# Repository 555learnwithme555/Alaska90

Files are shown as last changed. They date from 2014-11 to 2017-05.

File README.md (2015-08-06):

# Alaska90 3D printer design
This is the Alaska90, an enormous 3D printer.  It's not a tabletop machine--it's the size of a table!

Main features:
* 600mm x 500mm x 600mm build volume (24 inch x 20 inch x 24 inch), to construct models as big as a few feet on each side.
* Frame is built from 3/4 inch plywood, and parts are secured using large 1/4 inch hex head bolts (instead of M4 screws).
* Uses heavy 16mm steel rods, so it's rigid enough to mill wood with a small dremel tool.
* Support rods are moved inward, to gauss points, to better support the 24 inch x 24 inch bed.

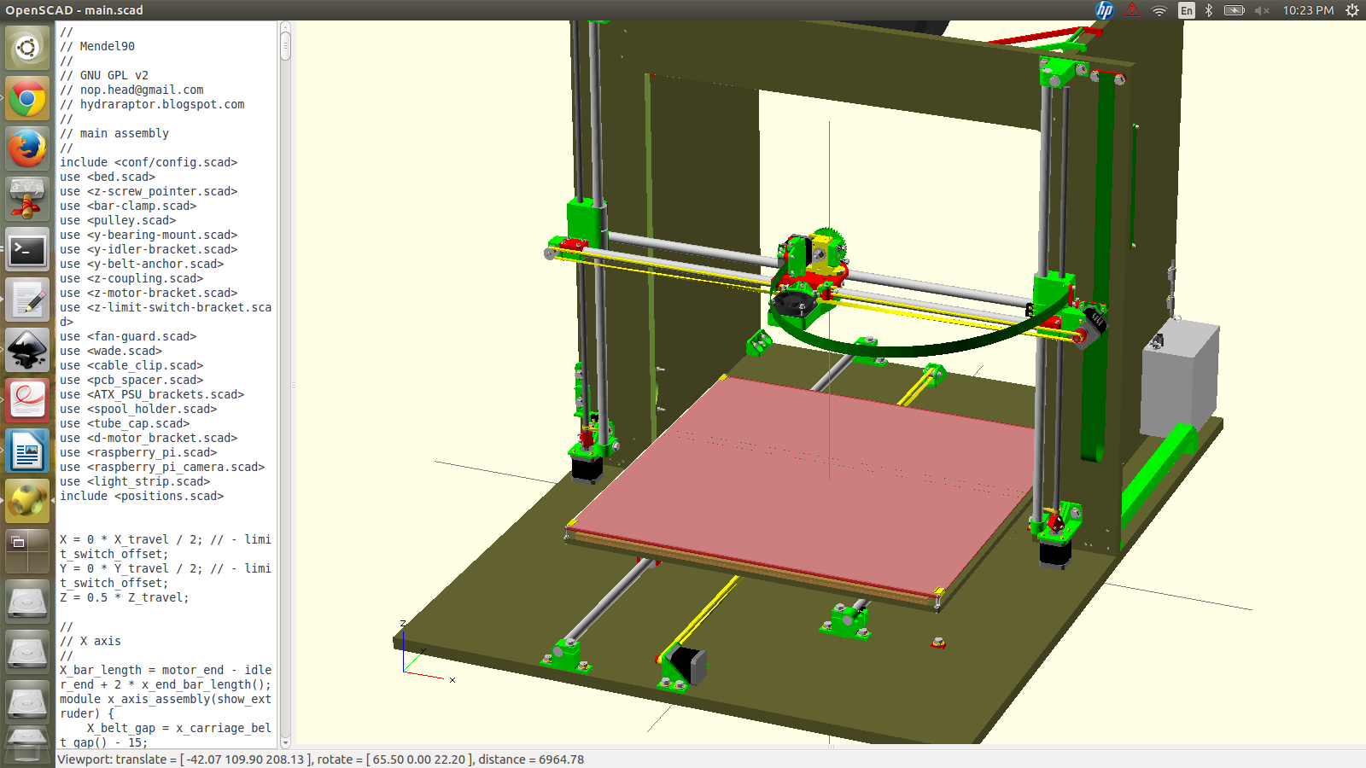
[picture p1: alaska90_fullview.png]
3D rendering of Alaska90 3D printer

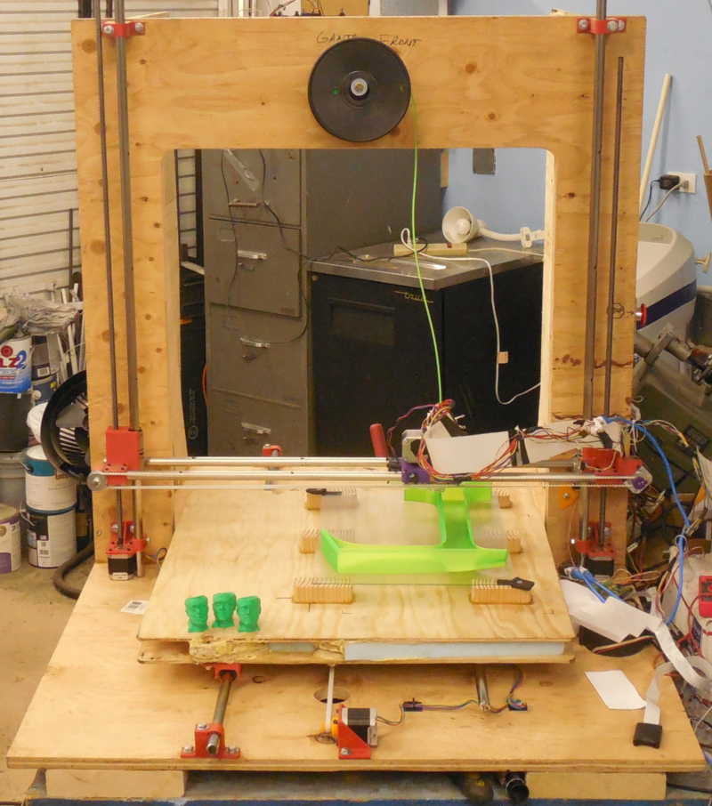
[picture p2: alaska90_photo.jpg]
Photograph of Alaska90 3D printer


This is an open source hardware design that started from Chris Palmer/nophead's amazing parametric CAD printer generator system Mendel90, with a number of changes by Dr. Orion Lawlor to accomodate the much larger machine.  This version is definitely "beta" quality, with several crude hacks in the OpenSCAD to make the STL parts work at the larger size.  Also, I laid out the frame holes by hand because I couldn't find a router big enough to cut the full 4ft x 3ft sheet, so the DXFs are likely to be somewhat inaccurate.

# Making giant 3D prints

There are a number of challenges in scaling up a 3D printer this big:

* Time per print.  At a fixed layer height, if you double the size of the object, the number of layers doubles, the time per perimeter doubles, and the time per infill quadruples.  This means the total time per print scales up quadratically even for completely hollow objects, and time is cubic for filled objects.  One workaround is to use large layer height, above 0.3mm, to reduce the number of layers.  You can also try to push the printer to deposit material faster by using a larger nozzle hole size, currently 0.5mm.
* Curl.  Without a heated bed and build chamber, a PLA object over a foot across will curl up off the build platform.

# Parts and suppliers

The original Mendel90 has a spectacularly detailed Bill-of-Materials (BOM) system that keeps track of every part needed, down to the last bolt and nut.  I tried to keep this updated--see [alaska90/bom/bom.txt](alaska90/bom/bom.txt)--but I probably didn't get it quite perfect, since much of the design was adapted on the fly.

## Mechanical parts & suppliers

I built the frame from 3/4" thick plywood, which I screwed and glued together rather than use 3D printed fixing blocks.  The base is built on an "H" shape of 2x8 lumber, glued to the base plywood, to increase stiffness and keep the machine up off the floor.

To reduce the moving mass of the bed while keeping it stiff, it was glued together as a "sandwich" with 5mm plywood on the top and bottom surfaces, and 1 inch thick blue XPS foam glued in the middle using one-part moisture cure urethane "Gorilla" glue.

http://www.amazon.com/LM16UU-Linear-Bearing-Bushing-linear/dp/B00AGCT6FW
	LM16UU linear bearings, one package of ten for $28

You need a total of six very straight and smooth steel rods:
	Two X axis rods, length 830mm (33 inches)
	Two Y axis rods, one long rod of length 1210mm (48 inches), and one short rod of length 692mm (28 inches).
	Two Z axis rods, length 760mm (30 inches)
Ideally, you'd start with five 36 inch rods (this is the standard length for "drill rod"), and add one 48 inch rod.

http://www.vxb.com/page/bearings/PROD/kit1008
	16mm hardened rod, 60" for $50.

I used 5/8 inch steel rods from an old foosball machine, which works since 5/8 inch is 15.83mm, but 16mm steel rods would fit the bearings with slightly less play.  In a machine this huge, deflection is going to dominate your positioning errors anyway.

http://smile.amazon.com/Rolled-Steel-Mandrel-Tubing-Length/dp/B000H9K3GU/
	5/8" OD, 0.40" ID, DOM and very smooth.  $15 for 36".

For the Z axis threaded rods, I used some 3/8 inch ACME threaded rod.  Normal 3/8 inch or 10mm threaded rod would probably work about equally well.

For the X and Y axes, I used T5 belts.  The cool kids are using GT2 belts nowadays, though!

http://smile.amazon.com/Meters-Timing-Perfect-RepRap-Mendel/dp/B00GVAOOUK/r
	5 meters T5 timing belt, $20

http://www.ebay.com/itm/T5-Aluminum-Timing-Pulleys-8-Tooth-5mm-Bore-for-RepRap-Prusa-Mendel-3D-Printer-/141217630049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
	T5 timing belt pulleys, 8 tooth, 5mm bore, $5

##Electrical Parts & Suppliers

You need five NEMA 17 stepper motors.  I was surprised to find the smaller steppers are quite strong enough to move this large machine, especially the Y axis, which needs to rapidly move a 10 pound table!

http://smile.amazon.com/gp/product/B00C43IW4C?psc=1&redirect=true&ref_=oh_aui_detailpage_o09_s00
	5x Kysan 1124090 stepper motors for $75

http://www.ebay.com/itm/0-3-0-35-0-4-0-5mm-Nozzle-for-RepRap-1-75-3mm-filament-J-Head-Jhead-MK-V-Hot-End-/361088211963
	$25 Ebay J-head hotend.  I picked 3mm filament and 0.5mm nozzle.

http://www.ebay.com/itm/Melzi-2-0-1284P-Reprap-Control-Mainboard-3-D-Printer-Controller-Main-Board-PCB-/121477844641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
	I used this $42 [Melzi controller board](http://reprap.org/wiki/Melzi).  
	
All the [stepper current limit potentiometers need to be cranked all the way](http://reprap.org/wiki/RepRapPro_Setting_Motor_Currents) for the tiny steppers to successfully push this large machine.  The Melzi stepper drivers tend to overheat when worked this hard, so I added a small squirrel cage fan blowing directly on them.

For printing PLA, I added a tiny 40mm case fan hanging between the X axis rods, by screwing M4 screws directly into the carriage.

I used a scrapped PC power supply to supply 12 volts (yellow and black wires) to the Melzi.  I added a big red emergency stop button to disconnect the power supply's green power-on wire from ground, turning the power supply off.

Much to my detriment, for my wiring I used a combination of rats-nest hand assembled wire bundles, which are messy and confusing; and RJ45 connectors, which are not very good at handling the 2-3 amp current to the steppers and hotend.  Nophead designed in neat brackets for ribbon cable, which would probably work better.

-------------------------- Original Mendel90 README -------------------
Limitations
-----------
Currently only supports mendel and sturdy machine variants, the huxley version needs more work.

Use
---
Add the directory of the OpenScad executable to your search path. OpenSCAD-2013.06 or later is required.
To get PDF versions of the sheet drawings add InkScape to your search path.

To make all the files for a machine run
```python
make_machine.py machine_name
```

To make just the bom, sheets or stls run bom.py, sheets.py or stls.py machine\_name.

machine\_name can be mendel or sturdy. To make your own variant copy scad\conf\mendel\_config.scad or scad\conf\sturdy\_config.scad to yourname\_config.scad.  Then run `make_machine.py yourname`.

To view the model of the whole machine, open scad\main.scad. It will take several minutes to render (about about 8 minutes on my computer) but after that you can pan and zoom it at reasonable speed and changes takes less time to render.  (Note: main.scad will only render correctly if conf\machine.scad exists, which is created by the make_machine.py script.)

To view a sub-assembly, open the individual scad files. Set the exploded flag in config.scad to make exploded views.

To get blender renders of all the parts put blender in your search path and run `render.py machine_name`.

Credits
-------
Fan model based on [this model](http://www.thingiverse.com/thing:8063) by MiseryBot, CC license.

[Sanguinololu model](http://www.thingiverse.com/thing:18606) by ax\_the\_b, CC license.

Spring taken from openscad example 20

x-end.scad and wade.scad use some elements of the Prusa ones by Josef Prusa, GPL license.

z_couplings originally based on [this model](http://www.thingiverse.com/thing:7153) by Griffin_Nicoll, GPL license.

Bearing holders originally based on [this model](http://www.thingiverse.com/thing:7755) by Jolijar, CC license.

InkCL.py based on [this code](http://kaioa.com/node/42)

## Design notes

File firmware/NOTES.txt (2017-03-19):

Flashing Alaska90 firmware to Melzi 2.0 board works like a 
"sanguino" arduino:
	- Use Arduino IDE 1.0.5:  ~/dev/hardware/arduino/ide/old/arduino-1.0.5/arduino

In 1.6.5, go to File -> Preferences -> Additional board manager URLs:
  https://raw.githubusercontent.com/Lauszus/Sanguino/master/package_lauszus_sanguino_index.json
Now go to Tools -> Boards -> Boards Manager. 
Scroll to the bottom, and "Install" the Sanguino.

Tools -> Boards -> Sanguino
Tools -> Processors -> ATmega 1284 or 1284P 16MHz

---------- The Hardware ---------
Sanguino (open source, ATmega 644P)
-> Sanguilino (includes steppers)
-> Melzi ("Joe Mosfet", ATmega 1284P, like Leonardo)
-> Melzi 2.0 (RepRapPro)

This is basically an Arduino Leonardo (ATMEGA1284P), with four A4988 stepper drivers (2A, 35V rated), and three RFP30N06LE MOSFETs (30A, 60V rated).  You use the Marlin/Sanguino firmware.
	http://reprap.org/wiki/Melzi

Must copy the Marlin_official/ArduinoAddons/Arduino_1.x.x/hardware/Sanguino directory into the arduino IDE/hardware folder (as of 1.0.5) for the Sanguino boards to show up.  Pick board "Sanguino W/ ATmega 1284p 16(?)MHz".
This only seems to work with the 1.0.5 IDE, not 1.6.x.

To edit the Melzi firmware, you need to install the AUTO-RESET jumper on the right side of the board.

http://www.youtube.com/watch?v=PQ807R1Nsio
Quint Boney uses Repetier Firmware on Melzi 2.0 electronics.

------------- Marlin --------------
Default baudrate is 250000.  Dropping to 115200.

eBay J clone Thermistor:
	57F -> 165 K ohms
	72F -> 100 K ohms
This crappy board's pull-up is 10Kohms, so I needed to manually adjust the table using the thermistor.xls spreadsheet.  I have no idea how close it is when hot, but it's pretty close when cold.  Using a 1K pull-up would be better, since the hot end 

Heater resistor: 12ohms, so about 12 watts at 12VDC.

The normal Arduino IDE flashes the firmware fine, although it takes a scary length of time to flash, and the LED no longer blinks.

pronterface takes an amazing 8 seconds to connect.
Using a 1K resistor as a fake thermistor results in a temperature reading of 198.4/5 C in Pronterface.  It should actually be 172.5 C, according to my thermistor table.  I need to meter the "10K" pullup to see what it really reads.  Turns out, it's like 9.8Kohms, but the problem was selecting the right table in Configuration.h.  With the right table, we're at 173.9/174.2, which is perfect.

Z speed: seems capped at 300mm/min (pretty slow!).  Fixed in firmware DEFAULT_MAX_FEEDRATE.

At acceleration of 100:
Up to 460mm/min works OK.
Z loses steps going up at 500, 600, or 700 mm/min.

At acceleration of 20, acceleration process is audible.  Steps still lost at 560 (only going up, and only now and then), and more definitely at 660.

Capping Z speed to 7 mm/sec, 460mm/min.  That's still over 1 minute for a full Z seek, but OK.

-------
To tune hotend:

M303 E0 S200 C4

---------------
I'd like to set up a sub-Melzi to drive the sandstruder.

I'm tempted to just tie across pin A1 from the mainmelzi to the submelzi.
Main would have it as the E1 step pin; sub would forward it to E0.
(sandstruder doesn't really do retract.)

~/dev/hardware/arduino/ide/old/arduino-1.0.5/arduino subMelzi/subMelzi.ino

The Melzi board bootloader(?) really does take 8 seconds to boot.  That's annoying.

-----------------
Two extruders is surprisingly easy to set up, and it works well.
Three extruders, E2 randomly dribbles whenever E1 is stepping.
Is this because "DIR" pins overlap for T1 and T2 somehow?

Trying to separate the T1 and T2 pins by more distance:
// Sub-melzi extruder 1: sandstruder
#define E1_STEP_PIN      30 // pin analog A1 (fake fastio.h pin numbers)
#define E1_DIR_PIN       29 // pin analog A2
#define E1_ENABLE_PIN      -1

// Sub-melzi extruder 2: tamper
#define E2_STEP_PIN      27 // pin analog A4
#define E2_DIR_PIN       28 // pin analog A3
#define E2_ENABLE_PIN      -1

---------------
Bumped up to 24V operation.  Re-tuning moves:

http://marlinfw.org/docs/gcode/M203.html

Dump current settings with M503

echo:Steps per unit:
echo:  M92 X53.33 Y53.33 Z1511.79 E519.11
echo:Maximum feedrates (mm/s):
echo:  M203 X600000.00 Y600000.00 Z10.00 E100.00
echo:Maximum Acceleration (mm/s2):
echo:  M201 X600000 Y600000 Z1000 E5000
echo:Acceleration: S=acceleration, T=retract acceleration
echo:  M204 S3000.00 T3000.00
echo:Advanced variables: S=Min feedrate (mm/s), T=Min travel feedrate (mm/s), B=minimum segment time (ms), X=maximum XY jerk (mm/s),  Z=maximum Z jerk (mm/s),  E=maximum E jerk (mm/s)
echo:  M205 S0.00 T0.00 B20000 X3.00 Z0.40 E3.00
echo:Home offset (mm):
echo:  M206 X0.00 Y0.00 Z0.00
echo:PID settings:
echo:   M301 P10.20 I0.63 D40.00

M201 sets max acceleration (mm/sec^2)
M203 sets max feedrate (mm/sec)

g1 x200 y200 f20000

'f' moves are mm/minute
firmware numbers are mm/second, off by 60x

Crazy fast, but still doesn't seem to lose steps at 19.6VDC:
M201 X60000 Y60000
M203 X60000 Y60000
g1 f60000
g1 x200 y200
g1 x300 y300

M201 X600000 Y600000

Too fast: loses steps at peak velocity:
M203 X600000 Y600000

Good and fast: 
M203 X60000 Y60000

g1 f600000
g1 x200 y200
g1 x300 y300

Noticably slower:
M201 X600 Y600

Slow ramp-up:
M201 X60 Y60

Actual active acceleration seems to be the M204:
At 19.6V, empty bed:
  M204 S60000 ; uncapped

Conservative:
M201 X3000 Y1000 Z100 E
M203 X1000 Y1000 Z8   E
Midrange:
M201 Y1500 X5000 

Y change: 
M201 Y1000
M203 Y1100 
G1 F100000
G1 Y100 
G1 Y400
velocity:
1100 fine
5000 fine (never hits peak at 1000 accel)

accel:
1000 slow and careful (correct long-term speed)
2000 might lose one occasional step
2300 loses a tiny block of steps at each run (and still loses a few at 24V)
2500 loses a few steps
3000 loses most steps
10000 loses all steps in Y axis

X change:
M201 X5000
M203 X1100 
G1 F100000
G1 X100 
G1 X400
vel:
1000 fine
1100 fine
1200 loses steps in big clunky chunks (?!)
2000 loses steps
5000 loses steps
accel:
1000 slow and fine
3000 fine
5000 seems reliable
6000 still reliable
7000 loses on return
10000 loses most steps

Z change: big limit is feedrate
M201 Z100
M203 Z8 
G1 Z110
G1 Z130
Acceleration M201 Z10 is very slow. Z100 is about normal.  Z1000 looks same.
Feedrate M203 Z100 moves too fast
8 is probably safe
10 is fine
12, 13, 15 lose steps (!)
20 hits resonance and loses steps

Actual used acceleration is smaller of:
  M204 Sxxxx global limit (combined X and Y?)
  M203 per-axis limit

Right thing is probably to leave S big, do work per-axis.

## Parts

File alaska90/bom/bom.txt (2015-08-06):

Vitamins:
          E                                                      
          x                                                      
          t                                                      
          r                                                      
          u                                                      
          d                                                      
          e                                                      
          r                                                      
                                                                 
          c  E                       X                       Z   
          o  x                                                   
          n  t              S        c                       l   
    E     n  r              p        a                       i   
    l     e  u              o     X  r           Y           m   
    e     c  d        P     o        r                       i   
    c  E  t  e        r     l     c  i           c           t   
 B  t  x  i  r     M  i           a  a  X  X     a  Y  Y        Z
 e  r  t  o        a  n     h  X  r  g        Y  r        Z  s   
 d  o  r  n  m  F  c  t     o     r  e  i  m     r  i  m     w  m
    n  u     o  r  h        l  a  i     d  o  a  i  d  o  a  i  o
 f  i  d  p  t  a  i  b  P  d  x  a  f  l  t  x  a  l  t  x  t  t
 a  c  e  c  o  m  n  e  s  e  i  g  a  e  o  i  g  e  o  i  c  o
 n  s  r  b  r  e  e  d  u  r  s  e  n  r  r  s  e  r  r  s  h  r
  |  |  |  |  |  |  |  | 1|  |  |  |  |  |  |  |  |  |  |  |  |  |  1 THS15 Aluminium clad resistor 10R
  |  |  |  |  |  |  |  | 1|  |  |  |  |  |  |  |  |  |  |  |  |  |  1 THS15 Aluminium clad resistor 4R7
  |  |  |  |  |  |  |  | 1|  |  |  |  |  |  |  |  |  |  |  |  |  |  1 PSU e.g. ALPINE500
  |  | 3|  |  |  |  |  |  | 4|  |  |  |  |  |  |  |  |  |  |  |  |  7 Ball bearing 608 8mm x 22mm x 7mm
  |  |  |  |  |  |  |  |  |  |  |  |  | 2|  |  |  | 2|  |  |  |  |  4 Ball bearing 624 4mm x 13mm x 5mm
  |  |  |  |  |  |  | 4|  |  |  |  |  |  |  |  |  |  |  |  |  |  |  4 19mm bulldog clip
  |  |  |  |  |  |  | 1|  |  |  |  |  |  |  |  |  |  |  |  |  |  |  1 PCB bed 615mm x 615mm
  |  |  |  |  |  |  |  |  |  | 1|  |  |  |  |  |  |  |  |  |  |  |  1 Belt T5 x 6mm x 1760mm
  |  |  |  |  |  |  |  |  |  |  |  |  |  |  | 1|  |  |  |  |  |  |  1 Belt T5 x 6mm x 1820mm
  |  |  |  |  |  |  | 2|  |  |  |  |  |  |  |  |  |  |  |  |  |  |  2 Corrugated cardboard 578mm x 618mm x 5mm
  |  |  |  |  |  |  | 4|  |  |  | 2|  |  |  |  |  |  |  |  |  |  |  6 M3 cap screw x 10mm
  |  | 3|  |  |  |  |  |  |  |  |  |  |  | 6|  | 8|  |  |  |  |  | 17 M3 cap screw x 16mm
  |  |  |  |  |  |  |  |  |  |  | 1|  |  | 2|  |  |  |  |  |  | 8| 11 M3 cap screw x 20mm
  | 4|  |  |  |  |  |  |  |  |  | 2|  |  |  |  |  |  |  |  |  |  |  6 M3 cap screw x 25mm
  |  |  |  |  |  |  |  |  |  |  |  |  | 8| 8|  |  |  |  |  |  |  | 16 M3 cap screw x 30mm
  |  |  |  | 2|  |  |  |  |  |  |  |  |  | 1|  |  |  |  |  |  |  |  3 M3 cap screw x 45mm
  |  |  |  |  |  |  |  |  |  |  |  | 4|  |  |  |  | 1|  |  |  |  |  5 M4 cap screw x 30mm
 4|  |  |  |  |  |  |  |  |  |  |  |  |  |  |  |  |  |  |  |  |  |  4 M4 cap screw x 35mm
  |  |  |  |  |  |  |  |  |  |  |  |  | 1|  |  |  |  |  |  |  |  |  1 M4 cap screw x 45mm
  |  |  | 1|  |  |  |  |  |  |  |  |  |  |  |  |  |  |  |  |  |  |  1 15 way D PCB mount plug
  |  |  |  |  |  |  |  |  |  |  |  |  |  | 1|  |  |  |  |  |  |  |  1 15 way D IDC socket
  |  |  |  |  |  |  |  |  |  |  |  | 1|  |  |  |  |  |  |  |  |  |  1 Fan 60mm x 15mm
  |  |  |  |  |  |  |  |  | 1|  |  |  |  |  |  |  |  |  |  |  |  |  1 Foam sponge 20mm x 20mm x 20mm
  |  |  |  | 1|  |  |  |  |  |  |  |  |  | 1|  |  |  | 1|  |  |  |  3 M3 grub screw x 6mm
  |  |  |  |  |  |  | 1|  |  |  |  |  |  |  |  |  |  |  |  |  |  |  1 Glass sheet 615mm x 603mm x 2mm
  |  |  |  |  |  |  | 4|  |  |  |  |  |  |  |  |  |  |  |  |  |  |  4 Hex male / female pillar M6.5 x 13mm
  |  | 3|  |  |  |  |  |  |  |  |  |  |  |  |  |  |  |  |  |  |  |  3 M3 hex screw x 10mm
  |  |  |  |  |  |  |  |  |  |  |  |  |  |  |  |  |  |  |  | 1|  |  1 M3 hex screw x 16mm
  |  | 2|  |  |  |  |  |  |  |  |  |  |  |  |  |  |  |  |  |  |  |  2 M4 hex screw x 20mm
  |  | 2|  |  |  |  |  |  |  |  |  |  |  |  |  |  |  |  |  |  |  |  2 M4 hex screw x 50mm
  |  | 1|  |  |  |  |  |  |  |  |  |  |  |  |  |  |  |  |  |  |  |  1 M8 hex screw x 60mm, hobbed at 25
  |  |  |  |  |  |  |  | 1|  |  |  |  |  |  |  |  |  |  |  |  |  |  1 IEC mains lead
  |  |  |  |  |  |  |  |  |  |  |  |  |  |  |  | 6|  |  |  |  |  |  6 1/4in hex screw x 16mm
  |  |  |  |  |  |  |  |  |  |  |  |  |  |  |  | 2|  |  |  |  |  |  2 1/4in hex screw x 20mm
  |  |  |  |  |39|  |  | 4| 2|  |  |  |  |  |12|  | 1| 4| 6| 2| 6| 76 1/4in hex screw x 25mm
  |  |  |  |  |  |  |  |  |  |  | 1|  | 2| 2|  | 3|  |  |  |  |  |  8 LM16UU linear bearing
  |  |  |  |  |  |  |  |  |  |  |  |  |  |  |  | 1|  |  |  |  |  |  1 MDF sheet 618mm x 618mm x 10mm
  |  |  |  |  | 2|  |  |  |  |  |  |  |  |  |  |  |  |  |  |  |  |  2 MDF sheet 532mm x 809mm x 19.5mm
  |  |  |  |  | 1|  |  |  |  |  |  |  |  |  |  |  |  |  |  |  |  |  1 MDF sheet 916mm x 1213mm x 19.5mm
  |  |  |  |  | 1|  |  |  |  |  |  |  |  |  |  |  |  |  |  |  |  |  1 MDF sheet 916mm x 809mm x 19.5mm
  | 1|  |  |  |  |  |  |  |  |  |  |  |  |  |  |  |  |  |  |  |  |  1 Melzi electronics
  |  |  | 1|  |  |  |  |  |  |  |  |  |  |  |  |  |  |  |  |  |  |  1 2 way Molex KK header
  |  |  | 1|  |  |  |  |  |  |  |  |  |  |  |  |  |  |  |  |  |  |  1 3 way Molex KK header
  |  |  |  | 1|  |  |  |  |  |  |  |  |  | 1|  |  |  | 1|  |  | 2|  5 NEMA17 x 48mm stepper motor
  |  |  |  |  |  |  |  |  |  |  |  |  |  |  |  |  |  |  | 2|  |  |  2 Brass nut M8
  |  | 3|  | 3|  |  |  |  |  |  | 1|  |  | 1|  |  |  | 1|  |  |  |  9 Nut M3
  |  | 2|  |  |  |  |  |  |  |  |  |  |  |  |  |  |  |  |  |  |  |  2 Nut M4
  |  | 2|  |  |  |  |  |  |  |  |  |  |  |  |  |  |  |  |  |  |  |  2 Nut M8
  |  |  |  |  |  |  |  |  |  |  | 4|  | 8|14|  | 8|  |  |  | 1| 8| 43 Nyloc nut M3
 4|  |  |  |  |  |  |  |  |  |  |  | 4| 1|  |  |  | 1|  |  |  |  | 10 Nyloc nut M4
  |  |  |  |  |  |  |  |  |  |  |  |  |  |  | 4| 8|  |  | 2|  | 2| 16 Nyloc nut M6.4
  |  |  |  |  |  |  |  |  |  |  |  |  |  | 2|  |  |  |  |  |  |  |  2 Nitrile O-ring 2.5mm x 1.6mm
  |  |  | 1|  |  |  |  |  |  |  |  |  |  |  |  |  |  |  |  |  |  |  1 Extruder connection PCB
  |  |  |  |  |  |  |  |  | 1|  |  |  |  |  |  |  |  |  |  |  |  |  1 PLA sample 3mm ~50m
  |  |  |  |  |  |  |  |  |  |  |  |  |  | 1|  |  |  |  |  |  |  |  1 Polypropylene strip 793mm x 18mm x 0.5mm
  |  |  |  |  |  |  |  |  |  |  |  |  |  | 1|  |  |  |  |  |  |  |  1 Polypropylene strip 984mm x 25mm x 0.5mm
  |  |  |  |  |  |  | 1|  |  |  |  |  |  |  |  |  |  |  |  |  |  |  1 Polypropylene strip 466mm x 33mm x 0.5mm
  |  |  |  |  |  |  |  |  |  |  |  |  |  | 2|  |  |  | 4|  |  | 8| 14 M3 pan screw x 8mm
  |  |  |  |  |  |  |  | 2|  |  |  |  |  |  |  |  |  |  |  |  |  |  2 6-32 pan screw x 9.5mm
  |  |  |  | 2|  |  |  | 4|  |  |  |  |  | 4| 2|  |  |  |  | 2|  | 14 No2 pan wood screw x 13mm
  |  |  |  |  |  |  |  |  |  |  |  |  |  | 1|  |  |  |  |  |  |  |  1 Ribbon cable 20 way 2147mm
  |  |  |  |  |  |  | 1|  |  |  |  |  |  |  |  |  |  |  |  |  |  |  1 Ribbon cable 26 way 576mm
  |  |  |  |  |  |  |  |  |  |  |  |  |  |  | 1|  |  |  |  |  |  |  1 Smooth rod 16mm x 1209mm
  |  |  |  |  |  |  |  |  |  |  |  |  |  |  | 1|  |  |  |  |  |  |  1 Smooth rod 16mm x 692mm
  |  |  |  |  |  |  |  |  |  |  |  |  |  |  |  |  |  |  | 2|  |  |  2 Smooth rod 16mm x 759mm
  |  |  |  |  |  |  |  |  |  | 2|  |  |  |  |  |  |  |  |  |  |  |  2 Smooth rod 16mm x 829mm
  |  | 1|  |  |  |  |  |  |  |  |  |  |  |  |  |  |  |  |  |  |  |  1 Smooth rod 8mm x 22mm
  | 1|  |  |  |  |  |  |  |  |  |  |  |  |  |  |  |  |  |  |  |  |  1 Micro SD card
  | 1|  |  |  |  |  |  |  |  |  |  |  |  |  |  |  |  |  |  |  |  |  1 Micro SD to USB adapter
  |  |  |  |  |  |  |  |  |  |  |  |  |  | 1| 1|  |  |  |  | 1|  |  3 Microswitch
  |  | 2|  |  |  |  |  |  |  |  |  |  |  |  |  |  |  |  |  |  |  |  2 Spring 7mm OD, 1mm gauge x 10mm long
  |  |  |  |  |  |  |  |  |  |  |  |  |  |  |  |  |  |  | 2|  |  |  2 Threaded rod M9.5 x 711mm
  |  |  |  |  |  |  |  | 1|  |  |  |  |  |  |  |  |  |  |  |  |  |  1 Heatshrink sleeving ID 10mm x 15mm
  |  |  |  |  |  |  | 2|  |  |  |  |  |  |  |  |  |  |  |  |  |  |  2 Heatshrink sleeving ID 1.6mm x 15mm
  | 2|  |  |  |  |  | 2| 3|  |  |  |  |  | 4|  |  |  |  |  |  |  | 11 Heatshrink sleeving ID 2.4mm x 15mm
  |  |  |  |  |  |  |  | 5|  |  |  |  |  |  |  |  |  |  |  |  |  |  5 Heatshrink sleeving ID 3.2mm x 15mm
  |  |  |  |  |  |  |  |  | 1|  |  |  |  |  |  |  |  |  |  |  |  |  1 PTFE tubing OD 4.6mm ID 3.84mm x 750mm
  |  |  |  |  |  |  |  | 2|  |  |  |  |  |  |  |  |  |  |  |  |  |  2 Heatshrink sleeving ID 6.4mm x 15mm
  |  |  |  |  |  |  | 2|  |  |  |  |  |  |  |  |  |  |  |  |  |  |  2 Heatshrink sleeving ID 6.4mm x 30mm
  |  |  |  |  |  |  |  |  |  |  |  |  |  |  |  |  |  |  |  |  | 2|  2 Neoprene tubing OD 8mm ID 5mm x 16mm
  |  |  | 2|  |  |  |  |  |  |  |  |  |  |  |  |  |  |  |  |  |  |  2 4 way terminal block
  |  |  |  |  |  |  | 1|  |  |  |  |  |  |  |  |  |  |  |  |  |  |  1 Epcos B57861S104F40 100K 1% thermistor
  | 1|  |  |  |  |  |  |  |  |  |  |  |  |  |  |  |  |  |  |  |  |  1 USB A to Mini B lead
  |  |  |  | 2|  |  |  |  |  |  |  |  |  | 4| 2|  |  |  |  | 2|  | 10 Washer M2.5 x 5.9mm x 0.5mm
  | 4| 3|  | 2|  |  | 4|  |  |  | 4|  | 8|21|  | 8|  | 4|  | 1|16| 75 Washer M3 x 7mm x 0.5mm
 4|  | 7|  |  |  |  |  | 2|  |  |  | 4| 2|  |  |  | 4|  |  |  |  | 23 Washer M4 x 9mm x 0.8mm
  |  |  |  |  |  |  |  |  |  |  |  |  | 2|  |  |  | 2|  |  |  |  |  4 Washer M5 x 20mm x 1.4mm
  |  |  |  |  |39|  |  | 4|14|  |  |  |  |  |12|14| 1| 4| 6| 2| 6|102 Washer M8 x 17mm x 1.6mm
  |  |  |  |  |  |  |  |  | 4|  |  |  |  |  |  |  |  |  |  |  |  |  4 Washer M8 x 30mm x 1.5mm
  |  |  |  |  |  |  |  |  |  | 2|  |  |  |  |  |  |  |  |  |  |  |  2 Wingnut M4
  |  |  |  |  |  |  |  |  |  |  |  |  |  |  |  |  |  |  |  | 2|  |  2 Rubber washer M3 x 10mm x 1.5mm
  |  |  |  |  |  |  | 1|  |  |  |  |  |  |  |  |  |  |  |  |  |  |  1 Black wire 32/0.2 length 635mm
  |  |  |  |  |  |  | 1|  |  |  |  |  |  |  |  |  |  |  |  |  |  |  1 Red wire 32/0.2 length 620mm
  | 4| 6|  |  |  |  |  |  |  |  |  |  |  | 2|  |  |  | 4|  |  | 8| 24 Star washer M3 x 0.5mm
  |  |  |  |  |  |  |  | 2|  |  |  |  |  |  |  |  |  |  |  |  |  |  2 Star washer M4 x 0.8mm
  |  | 1|  |  |39|  |  | 4| 2|  |  |  |  |  | 8|  | 1| 4| 4| 2| 4| 69 Star washer M8 x 1.6mm
  |  |  |  |  |  |  |  | 2|  |  |  |  |  |  |  |  |  |  |  |  |  |  2 Ziptie 100mm min length
  |  |  |  |  |  |  |  |  |  |  | 3|  |  |  |  | 3|  |  |  |  |  |  6 Ziptie 140mm min length

Printed:
  |  |  |  |  |  |  |  | 1|  |  |  |  |  |  |  |  |  |  |  |  |  |  1 atx_long_bracket.stl
  |  |  |  |  |  |  |  | 1|  |  |  |  |  |  |  |  |  |  |  |  |  |  1 atx_short_bracket.stl
  |  |  |  |  | 2|  |  |  |  |  |  |  |  |  |  |  |  |  |  |  |  |  2 cable_clip_AB.stl
  |  |  |  |  | 2|  |  |  |  |  |  |  |  |  |  |  |  |  |  |  |  |  2 cable_clip_AD.stl
  |  |  |  |  | 1|  |  |  |  |  |  |  |  |  |  |  |  |  |  |  |  |  1 cable_clip_CA.stl
  |  |  |  | 1|  |  |  |  |  |  |  |  |  |  |  |  |  |  |  |  |  |  1 d_motor_bracket.stl
  |  |  |  | 1|  |  |  |  |  |  |  |  |  |  |  |  |  |  |  |  |  |  1 d_motor_bracket_lid.stl
  |  |  |  |  |  |  |  |  |  |  |  |  |  | 1|  |  |  |  |  |  |  |  1 d_shell.stl
  |  |  |  |  |  |  |  |  |  |  |  |  |  | 1|  |  |  |  |  |  |  |  1 d_shell_lid.stl
  |  |  |  |  |  |  |  |  | 1|  |  |  |  |  |  |  |  |  |  |  |  |  1 dust_filter.stl
 1|  |  |  |  |  |  |  |  |  |  |  |  |  |  |  |  |  |  |  |  |  |  1 fan_guard.stl
  |  |  |  |  |10|  |  |  |  |  |  |  |  |  |  |  |  |  |  |  |  | 10 fixing_block.stl
  | 4|  |  |  |  |  |  |  |  |  |  |  |  |  |  |  |  |  |  |  |  |  4 pcb_spacer.stl
  |  |  |  |  |  |  |  |  |  |  |  |  |  | 1|  |  |  | 1|  |  |  |  2 pulley.stl
  |  |  |  |  |  |  |  |  |  |  |  |  |  | 1|  |  |  |  |  |  |  |  1 ribbon_clamp_14_33.stl
  |  |  |  |  |  |  |  |  |  |  |  |  |  | 1|  |  |  |  |  |  |  |  1 ribbon_clamp_14_33NB.stl
  |  |  |  |  |  |  |  |  |  |  |  |  |  | 1|  |  |  |  |  |  |  |  1 ribbon_clamp_20_33.stl
  |  |  |  |  | 1|  |  |  |  |  |  |  |  |  |  |  |  |  |  |  |  |  1 ribbon_clamp_20_66.stl
  |  |  |  |  | 1|  |  |  |  |  |  |  |  |  |  | 1|  |  |  |  |  |  2 ribbon_clamp_26_66.stl
  |  |  |  |  |  |  |  |  |  |  |  |  |  |  |  | 1|  |  |  |  |  |  1 ribbon_clamp_26_66N.stl
  |  |  |  |  |  |  |  |  | 2|  |  |  |  |  |  |  |  |  |  |  |  |  2 spool_bracket_female.stl
  |  |  |  |  |  |  |  |  | 2|  |  |  |  |  |  |  |  |  |  |  |  |  2 spool_bracket_male.stl
  |  | 1|  |  |  |  |  |  |  |  |  |  |  |  |  |  |  |  |  |  |  |  1 wades_big_gear.stl
  |  | 1|  |  |  |  |  |  |  |  |  |  |  |  |  |  |  |  |  |  |  |  1 wades_block.stl
  |  | 1|  |  |  |  |  |  |  |  |  |  |  |  |  |  |  |  |  |  |  |  1 wades_gear_spacer.stl
  |  | 1|  |  |  |  |  |  |  |  |  |  |  |  |  |  |  |  |  |  |  |  1 wades_idler_block.stl
  |  |  |  | 1|  |  |  |  |  |  |  |  |  |  |  |  |  |  |  |  |  |  1 wades_small_gear.stl
  |  |  |  |  |  |  |  |  |  |  | 1|  |  |  |  |  |  |  |  |  |  |  1 x_belt_clamp.stl
  |  |  |  |  |  |  |  |  |  |  | 1|  |  |  |  |  |  |  |  |  |  |  1 x_belt_grip.stl
  |  |  |  |  |  |  |  |  |  |  | 1|  |  |  |  |  |  |  |  |  |  |  1 x_belt_tensioner.stl
  |  |  |  |  |  |  |  |  |  |  | 1|  |  |  |  |  |  |  |  |  |  |  1 x_carriage.stl
  |  |  |  |  |  |  |  |  |  |  |  | 1|  |  |  |  |  |  |  |  |  |  1 x_carriage_fan_bracket.stl
  |  |  |  |  |  |  |  |  |  |  |  | 1|  |  |  |  |  |  |  |  |  |  1 x_carriage_fan_duct.stl
  |  |  |  |  |  |  |  |  |  |  |  |  | 2| 2|  |  |  |  |  |  |  |  4 x_end_clamp.stl
  |  |  |  |  |  |  |  |  |  |  |  |  | 1|  |  |  |  |  |  |  |  |  1 x_idler_bracket.stl
  |  |  |  |  |  |  |  |  |  |  |  |  |  | 1|  |  |  |  |  |  |  |  1 x_motor_bracket.stl
  |  |  |  |  |  |  |  |  |  |  |  |  |  | 1|  |  |  |  |  |  |  |  1 x_motor_ribbon_bracket.stl
  |  |  |  |  |  |  |  |  |  |  |  |  |  |  | 3|  |  |  |  |  |  |  3 y_bar_clamp.stl
  |  |  |  |  |  |  |  |  |  |  |  |  |  |  | 1|  |  |  |  |  |  |  1 y_bar_clamp_switch.stl
  |  |  |  |  |  |  |  |  |  |  |  |  |  |  |  | 3|  |  |  |  |  |  3 y_bearing_mount.stl
  |  |  |  |  |  |  |  |  |  |  |  |  |  |  |  | 1|  |  |  |  |  |  1 y_belt_anchor.stl
  |  |  |  |  |  |  |  |  |  |  |  |  |  |  |  | 1|  |  |  |  |  |  1 y_belt_anchor_toothed.stl
  |  |  |  |  |  |  |  |  |  |  |  |  |  |  |  | 1|  |  |  |  |  |  1 y_belt_clip.stl
  |  |  |  |  |  |  |  |  |  |  |  |  |  |  |  | 1|  |  |  |  |  |  1 y_belt_clip_toothed.stl
  |  |  |  |  |  |  |  |  |  |  |  |  |  |  |  |  | 1|  |  |  |  |  1 y_idler_bracket.stl
  |  |  |  |  |  |  |  |  |  |  |  |  |  |  |  |  |  | 1|  |  |  |  1 y_motor_bracket.stl
  |  |  |  |  |  |  |  |  |  |  |  |  |  |  |  |  |  |  | 2|  |  |  2 z_bar_clamp.stl
  |  |  |  |  |  |  |  |  |  |  |  |  |  |  |  |  |  |  |  |  | 4|  4 z_coupling.stl
  |  |  |  |  |  |  |  |  |  |  |  |  |  |  |  |  |  |  |  | 1|  |  1 z_limit_switch_bracket.stl
  |  |  |  |  |  |  |  |  |  |  |  |  |  |  |  |  |  |  |  |  | 1|  1 z_motor_bracket_lhs.stl
  |  |  |  |  |  |  |  |  |  |  |  |  |  |  |  |  |  |  |  |  | 1|  1 z_motor_bracket_rhs.stl
  |  |  |  |  |  |  |  |  |  |  |  |  |  |  |  |  |  |  | 2|  |  |  2 z_screw_pointer.stl

Sub-assemblies:
  1 bed_fan_assembly
  1 electronics_assembly
  1 extruder_assembly
  1 extruder_connection_pcb_assembly
  1 extruder_motor_assembly
  1 frame_assembly
  1 machine_assembly
  1 print_bed_assembly
  1 psu_assembly
  1 spool_holder_assembly
  1 x_axis_assembly
  1 x_carriage_assembly
  1 x_carriage_fan_assembly
  1 x_idler_assembly
  1 x_motor_assembly
  1 y_axis_assembly
  1 y_carriage_assembly
  1 y_idler_assembly
  1 y_motor_assembly
  1 z_axis_assembly
  1 z_limit_switch_assembly
  2 z_motor_assemblies

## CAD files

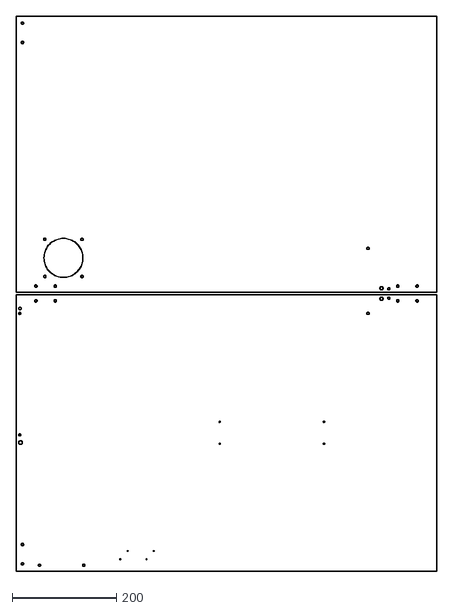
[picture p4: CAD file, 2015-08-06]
alaska90/sheets/frame_stays.dxf
809.0 x 1067.0

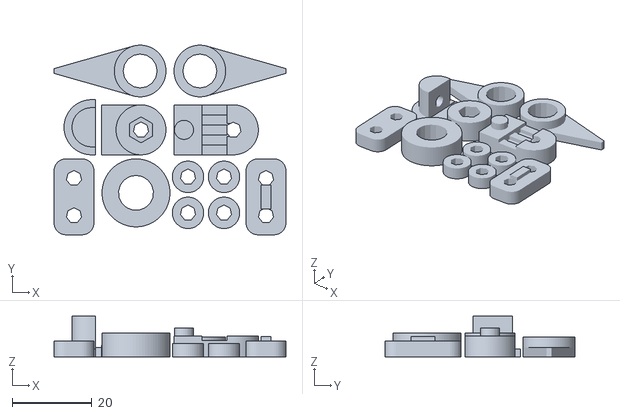
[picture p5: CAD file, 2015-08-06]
alaska90/stls/printed/small_bits.stl
58.0 x 47.4 x 10.2

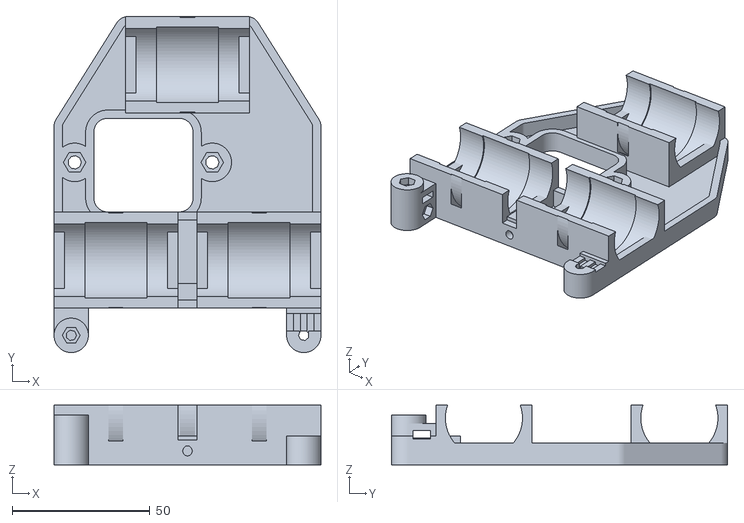
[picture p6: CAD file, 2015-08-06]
alaska90/stls/x_carriage.stl
97.0 x 122.1 x 21.7

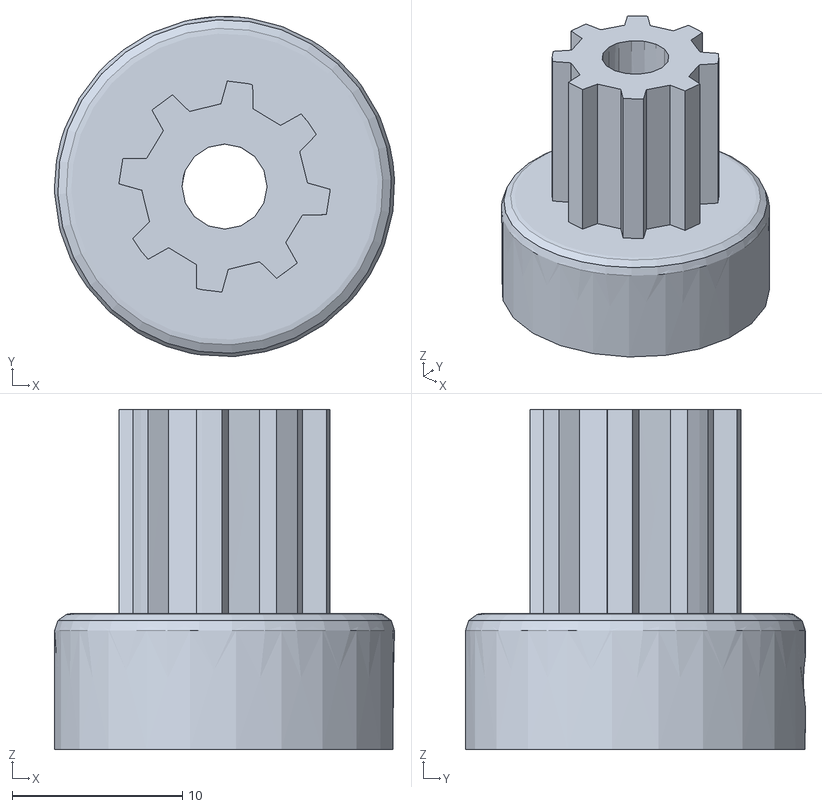
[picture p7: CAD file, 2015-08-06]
imported_stls/pulley_meatier/pulley.stl
20.0 x 20.0 x 20.0

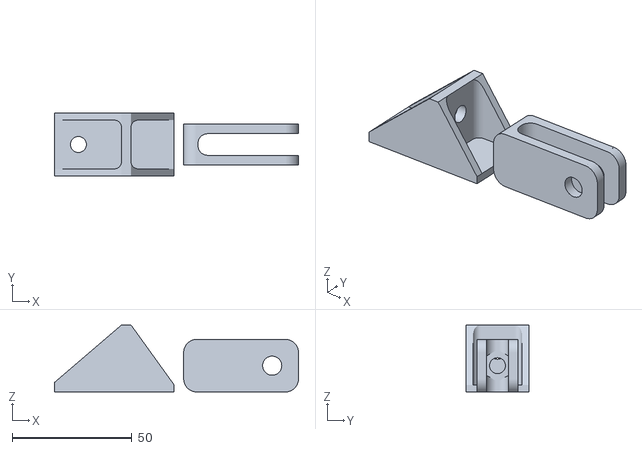
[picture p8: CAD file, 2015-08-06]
scad/y_adjustable_holder.stl
102.0 x 26.4 x 28.0

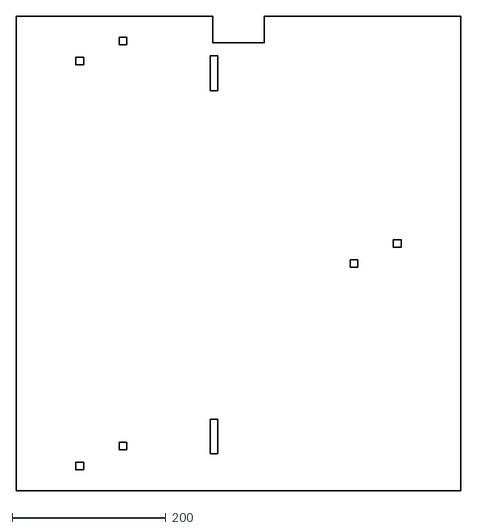
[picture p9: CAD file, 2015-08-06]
alaska90/sheets/y_heatshield.dxf
578.0 x 618.0

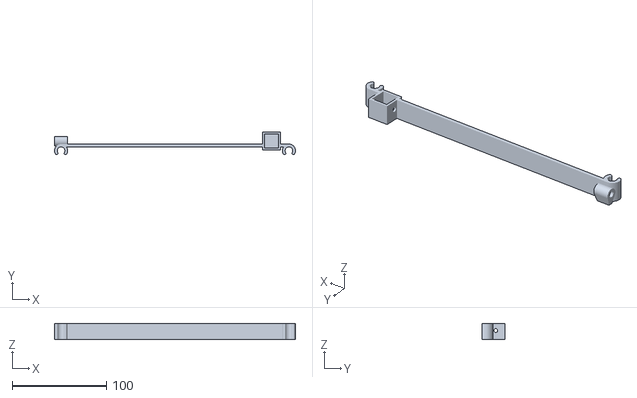
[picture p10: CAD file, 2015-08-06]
alaska90/stls/printed/dust_filter.stl
256.0 x 23.9 x 17.0

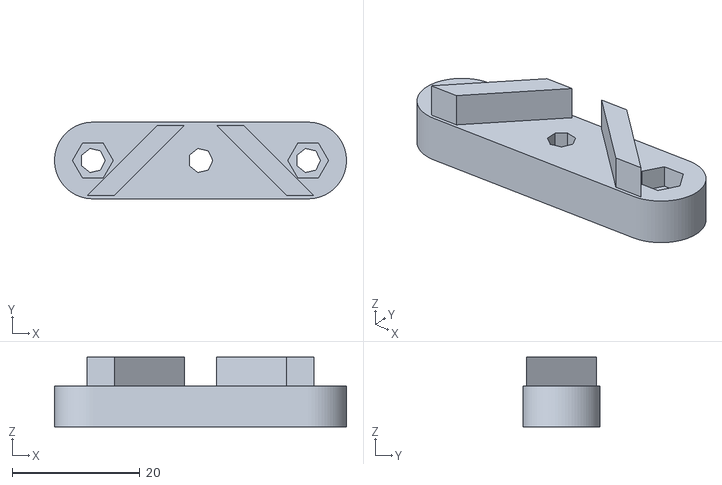
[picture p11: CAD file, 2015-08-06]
alaska90/stls/x_motor_ribbon_bracket.stl
45.7 x 12.0 x 10.9

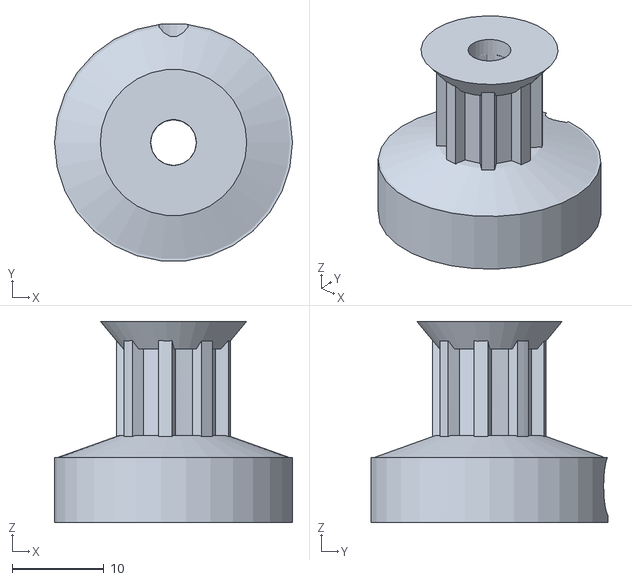
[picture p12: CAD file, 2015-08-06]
imported_stls/pulley_meatier/pulley_meatier.stl
26.0 x 25.9 x 22.0

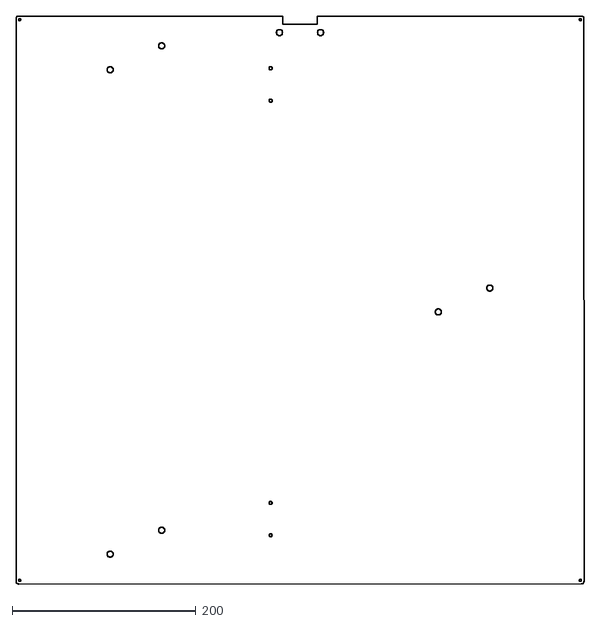
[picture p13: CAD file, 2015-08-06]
alaska90/sheets/y_carriage.dxf
618.0 x 618.0

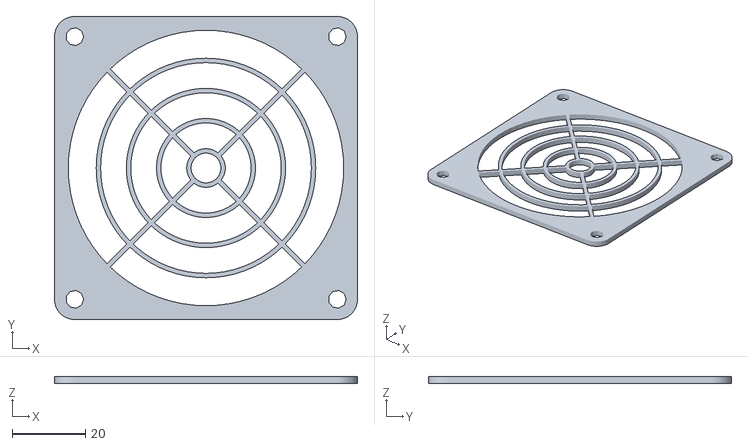
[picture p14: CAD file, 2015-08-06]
alaska90/stls/printed/fan_guard.stl
82.5 x 82.5 x 2.00

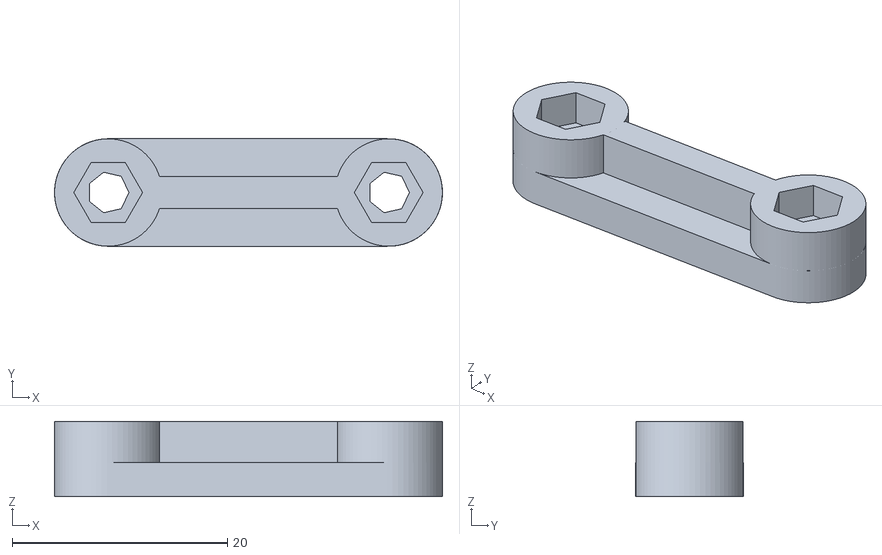
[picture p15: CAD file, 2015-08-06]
alaska90/stls/ribbon_clamp_14_33NB.stl
36.1 x 10.00 x 7.01

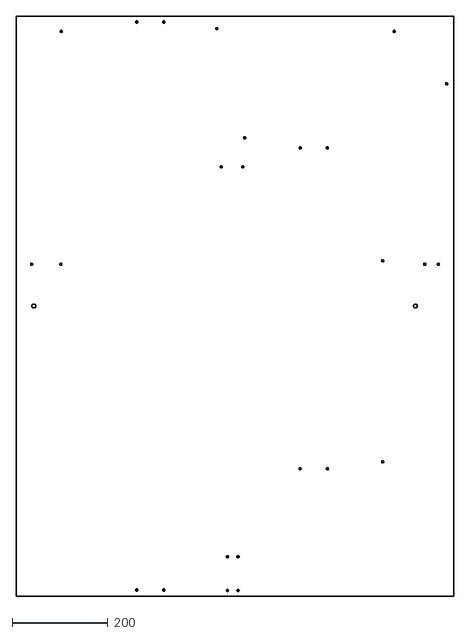
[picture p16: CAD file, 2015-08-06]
alaska90/sheets/frame_base.dxf
915.5 x 1213.0

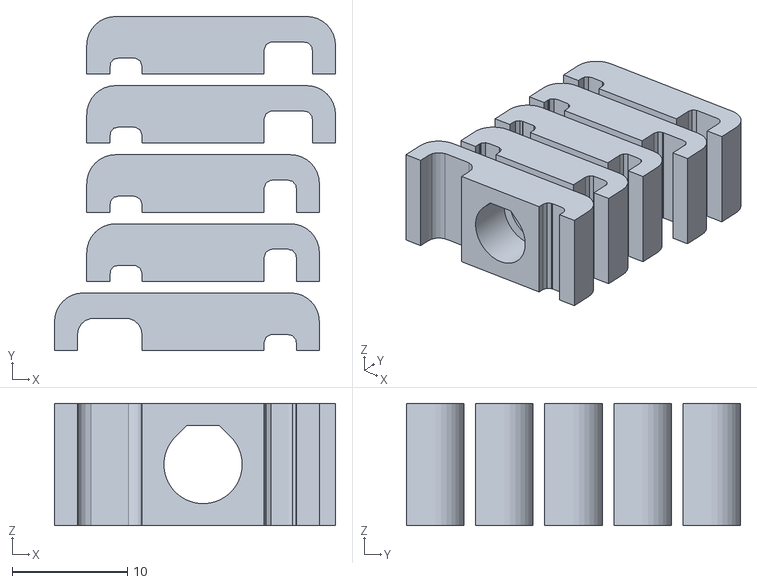
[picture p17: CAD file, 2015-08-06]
alaska90/stls/printed/cable_clips.stl
24.4 x 29.0 x 10.6

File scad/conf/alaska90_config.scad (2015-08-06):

//
// Mendel90
//
// GNU GPL v2
// nop.head@gmail.com
// hydraraptor.blogspot.com
//
// Configuration file
//
echo("Alaska90:");

Z_bearings = LM16UU; // 16mm == 5/8" foosball shaft, and same diameter as 30x40T CNC cutter
Y_bearings = LM16UU;
X_bearings = LM16UU;

X_motor = NEMA17;
Y_motor = NEMA17;
Z_motor = NEMA17;

hot_end = JHeadMk5clone; // an eBay copy, at least!

X_travel = 605; // 24"
Y_travel = 590; // 24" (trimmed to get total base length below 48")
Z_travel = 605; // 23" (trimmed to get total Z at about 32")

bed_depth = 615; // trimmed to leave some meat over gantry
bed_width = 615;
bed_pillars = QIx13_pillar; // M3x20_pillar;
bed_glass = glass2;
bed_thickness = pcb_thickness + sheet_thickness(bed_glass);    // PCB heater plus glass sheet
bed_holes = [bed_width-5, bed_depth-5];

base = MDF18;
base_corners = 0;

frame = MDF18;
frame_corners = 0;
frame_nuts = false;

pulley_type = T5x8_plastic_pulley;

case_fan = fan80x38;
psu = ALPINE500;
//psu = KY240W;
controller = Melzi; // 2.0, from eBay
//controller = Sanguinololu;
spool = spool_300x85;
bottom_limit_switch = true;
top_limit_switch = false;

single_piece_frame = true;
stays_from_window = false;

Y_carriage = MDF10;

X_belt = T5x6;
Y_belt = T5x6;

motor_shaft = 5;


Y_carriage_depth = bed_holes[1] + 8;
Y_carriage_width = bed_holes[0] + 8;


/*
// Z axis: 1/2" ACME rod, 10tpi looks way too big to fit in Z endpieces.
Z_screw_dia = 12.6;            
Z_nut_radius = 11; // M8_nut_radius;
Z_nut_depth = 12.25; // M8_nut_depth;
// Z_nut = M8_nut;
*/

// Z axis: 3/8" ACME rod
Z_screw_dia = 9.5;            
Z_nut_radius = 20.0/2; // "radius" == point to point, not across flats!
Z_nut_depth = 9.2; 
Z_nut = M8_nut; // only for inventory


//
// Default screw use where size doesn't matter
//
cap_screw = QI_hex_screw;
hex_screw = QI_hex_screw;
//
// Screw for the frame and base
//
frame_soft_screw = QI_hex_screw; // No6_screw;               // Used when sheet material is soft, e.g. wood
frame_thin_screw = QI_hex_screw; // M4_cap_screw;            // Used with nuts when sheets are thin
frame_thick_screw = QI_hex_screw; // M4_pan_screw;           // Used with tapped holes when sheets are thick and hard, e.g. plastic or metal
//
// Feature sizes
//
default_wall = 4;
thick_wall = 5;

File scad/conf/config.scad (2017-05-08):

//
// Mendel90
//
// GNU GPL v2
// nop.head@gmail.com
// hydraraptor.blogspot.com
//
// Configuration file
//

function sqr(x) = x * x;            // shortcut

bom = $bom == undef ? 0: $bom;                 // 0 no bom, 1 assemblies and stls, 2 vitamins as well
exploded = $exploded == undef ? 0 : $exploded; // 1 for exploded view

show_jigs = true;               // show printed jigs required to build the machine
show_support = true;            // show support structures, must be set when generating STLs

// Real-world colors for various parts & vitamins
use_realistic_colors = false;    // true for "real" colors, false for "distinct" colors (useful during design and for build instructions)
printed_plastic_color = "blue";
cable_strip_real_color = "fuchsia";
belt_real_color = "yellow";
bulldog_real_color ="black";

eta = 0.03;                     // small fudge factor to stop CSG barfing on coincident faces.
$fa = 5;
$fs = 0.5;

//
// Hole sizes
//
No2_pilot_radius = 1.7 / 2;       // self tapper into ABS
No4_pilot_radius = 2.0 / 2;       // wood screw into soft wood
No6_pilot_radius = 2.0 / 2;       // wood screw into soft wood

No2_clearance_radius = 2.5 / 2;
No4_clearance_radius = 3.5 / 2;
No6_clearance_radius = 4.0 / 2;

M2_tap_radius = 1.6 / 2;
M2_clearance_radius = 2.4 / 2;
M2_nut_trap_depth = 2.5;

M2p5_tap_radius = 2.05 / 2;
M2p5_clearance_radius= 2.8 / 2;   // M2.5
M2p5_nut_trap_depth = 2.5;

M3_tap_radius = 2.5 / 2;
M3_clearance_radius = 3.3 / 2;
M3_nut_radius = 6.5 / 2;
M3_nut_trap_depth = 3;

M4_tap_radius = 3.3 / 2;
M4_clearance_radius = 2.2;
M4_nut_radius = 8.2 / 2;
M4_nut_trap_depth = 4;

M5_tap_radius = 4.2 / 2;
M5_clearance_radius = 5.3 / 2;
M5_nut_radius = 9.2 / 2;
M5_nut_depth = 4;

M6_tap_radius = 5 / 2;
M6_clearance_radius = 6.4 / 2;
M6_nut_radius = 11.6 / 2;
M6_nut_depth = 5;

M8_tap_radius = 6.75 / 2;
M8_clearance_radius = 8.4 / 2;
M8_nut_radius = 15.4 / 2;
M8_nut_depth = 6.5;

cnc_tool_dia = 2.4;
layer_height = 0.4;
filament_width = layer_height * 1.5;
min_wall = 2 * filament_width + eta;
part_base_thickness = 5;;           // The thickness of things screwed to the frame

pcb_thickness = 1.6;
feed_tube_rad = 5 / 2;              // Filament feed tube
feed_tube_tape_rad = 6.2 / 2;
feed_tube_tape = 12;
nozzle_length = 54;                 // how far nozzle is below top of carriage


include <colors.scad>
include <utils.scad>
include <vitamins.scad>

endstop_wires    = [2, 1.4, "A"];   // 7 strands of 0.2
motor_wires      = [4, 1.4, "B"];
bed_wires        = [2, 2.8, "C"];   // 13A mains cable
fan_motor_wires  = [6, 1.4, "D"];   // fan and motor wires along top of gantry
two_motor_wires  = [8, 1.4,,"E"];   // Y and Z motors
thermistor_wires = endstop_wires;

endstop_wires_hole_radius = wire_hole_radius(endstop_wires);
motor_wires_hole_radius = wire_hole_radius(motor_wires);
two_motor_wires_hole_radius = wire_hole_radius(two_motor_wires);
fan_motor_wires_hole_radius = wire_hole_radius(fan_motor_wires);
bed_wires_hole_radius = wire_hole_radius(bed_wires);
thermistor_wires_hole_radius = wire_hole_radius(thermistor_wires);

cnc_sheets = false;                 // If sheets are cut by CNC we can use slots, etc instead of just round holes
base_nuts = false;                  // Need something under the base if using nuts
clip_handles = true;
include_fan = false;
squeeze = false;                    // Bodge to make Huxley as small as possible without affecting dibond kits
part_fan = fan60x15;
raspberry_pi = false;               // Raspberry pi mounted on PSU
raspberry_pi_camera = false;        // RPI camera on bar across the back
light_strip = false;
include <machine.scad>              // this file is generated from the command line parameter to include one of the machine configs

screw_clearance_radius = screw_clearance_radius(cap_screw);
nut = screw_nut(cap_screw);
nut_radius = nut_radius(nut);
nut_trap_depth = nut_trap_depth(nut);
washer = screw_washer(cap_screw);

bearing_clamp_tab = cnc_sheets ? (nut_radius(nut) + 3 * filament_width) * 2 : washer_diameter(washer) + 2;   // how much the lugs stick out and their width
bearing_clamp_tab_height = 4;           // thickness of the lugs

hole_edge_clearance = 5;                // how close a hole can be to the edge of a sheet
base_clearance = cnc_sheets ? 1 : 2;    // how close we get to the edge of the base
axis_end_clearance = cnc_sheets ? 1 : 2;// how close we get to the end of an axis
limit_switch_offset = 1;                // the over travel to reach the limit switch
X_carriage_clearance = 2;               // how close the X carriage is to the XZ plane
                                        // how close the Y carriage is to the window in the XZ plane
Y_carriage_clearance = 2 + (clip_handles ? (bulldog_handle_length(small_bulldog) - (Y_carriage_width - bed_width) / 2) : 0);
Z_clearance = 10;                       // How close the top of the object gets to the gantry
belt_clearance = 0.2;                   // clearance of belt clamp slots

X_bar_dia = X_bearings[2];      // rod sizes to match the bearings
Y_bar_dia = Y_bearings[2];
Z_bar_dia = Z_bearings[2];

Y_idler_bearing = BB624;
X_idler_bearing = BB624;

extruder_ways = 4 + 6 + 2 + 1 + 1;      // motor + heater(x3) + thermistor + probe + fan = 14
x_end_ways = extruder_ways + 4 + 2;     // motor plus limit switch = 20
bed_ways = 24 + 2;                      // twelve each way for the current plus a thermistor

module wire_hole_or_slot(r) {
    if(cnc_sheets)
        rotate([0, 0, 90])
            slot(r = r, h = 100, l = 2 * r);
    else
        translate([0, r + hole_edge_clearance, 0])
            wire_hole(r);
}

// z_bar_offset is the X distance between the Z motor centerline and the Z smooth rod centerline
function z_bar_offset() = max(
	round(NEMA_width(Z_motor)) / 2,  // original
	Z_bearings[0]/2+Z_nut_radius+2 // modified for big guide rods and small motors
);

base_screw = sheet_is_soft(base) ? frame_soft_screw : (base_nuts ? frame_thin_screw : frame_thick_screw);
base_nut = base_nuts ? screw_nut(base_screw) : false;
base_nut_traps = base_nuts && cnc_sheets;
base_washer = screw_washer(base_screw);
base_screw_length = base_nuts ? screw_longer_than(
                                    sheet_thickness(base)
                                    + part_base_thickness +
                                    (cnc_sheets ? 1 : 2) * washer_thickness(base_washer)
                                    + nut_thickness(base_nut, true)
                                  )
                              : screw_shorter_than(
                                    sheet_thickness(base)
                                    + part_base_thickness
                                    + 2 * washer_thickness(base_washer)
                                 );


frame_screw = sheet_is_soft(frame) ? frame_soft_screw : (frame_nuts ? frame_thin_screw : frame_thick_screw);
frame_nut = frame_nuts ? screw_nut(frame_screw) : false;
frame_nut_traps = frame_nuts && cnc_sheets;
frame_washer = screw_washer(frame_screw);
frame_screw_length = frame_nuts ? screw_longer_than(
                                      sheet_thickness(frame)
                                      + part_base_thickness +
                                      (cnc_sheets ? 1 : 2) * washer_thickness(frame_washer)
                                      + nut_thickness(frame_nut, true)
                                  )

                                : screw_shorter_than(
                                      sheet_thickness(frame)
                                      + part_base_thickness
                                      + 2 * washer_thickness(frame_washer)
                                  );

echo("base screw length", base_screw_length);
echo("frame screw length",frame_screw_length);



module frame_screw(thickness) {
    if(frame_nuts && cnc_sheets) {
        nut(frame_nut, true);
        translate([0, 0, -sheet_thickness(frame) - thickness])
            rotate([180, 0, 0])
                screw_and_washer(frame_screw, frame_screw_length);
    }
    else {
        screw_and_washer(frame_screw, frame_screw_length, !frame_nuts);
        if(frame_nuts)
            translate([0, 0, -sheet_thickness(frame) - thickness])
                rotate([180, 0, 0])
                    nut_and_washer(frame_nut, true);
    }
}

module frame_screw_hole() {
    cylinder(r = frame_nuts ? screw_clearance_radius(frame_screw) : screw_pilot_hole(frame_screw), h = 100, center = true);
}
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

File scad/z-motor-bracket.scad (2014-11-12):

//
// Mendel90
//
// GNU GPL v2
// nop.head@gmail.com
// hydraraptor.blogspot.com
//
// Fastens the Z motor to the gantry
//
include <conf/config.scad>
include <positions.scad>
use <z-coupling.scad>

corner_rad = 5;
length = z_motor_bracket_width();  // OSL
thickness = 4;
back_thickness = part_base_thickness + (frame_nut_traps ? nut_trap_depth(frame_nut) : 0);
back_height = 32; // 24; // OSL
big_hole = NEMA_big_hole(Z_motor);
clamp_height = washer_diameter(washer) + 3;
clamp_thickness = bar_clamp_band;
clamp_screw_clearance = 2;
clamp_length = Z_bar_dia / 2 + bar_clamp_tab - 2;
gap = 1.5;

clamp_width = Z_bar_dia + 2 * clamp_thickness;

clamp_x = clamp_length - bar_clamp_tab / 2;

function z_motor_bracket_height() = back_height;

module z_motor_bracket_orient() {
    translate([z_bar_offset(),0,0]) {
        rotate([0,0,86]) {
          child();
        }
    }
}


module z_motor_bracket(y_offset, rhs) {
    width = y_offset + length / 2;
    cutout = y_offset - length / 2 - part_base_thickness;

    stl(rhs? "z_motor_bracket_rhs" : "z_motor_bracket_lhs");
        color(z_motor_bracket_color) {
            difference() {
                union() {
                    //
                    // main body
                    //
                    translate([0, width / 2 - length / 2, back_height / 2])
                        difference() {
                            cube([length, width, back_height], center = true);
                            translate([0, -back_thickness, thickness])
                                cube([length + 1, width, back_height], center = true);
                        }
                    //
                    // Bracing webs
                    //
                    for(x = [length / 2 - 2 * z_slot_inset - thickness / 2, -(length / 2 - 2 * z_slot_inset - thickness / 2)])
                        translate([x, y_offset - back_thickness + eta, thickness - eta])
                            rotate([90, 0, -90])
                                right_triangle(width = y_offset - back_thickness - big_hole, height = back_height - thickness, h = thickness);
                    //
                    // bar clamp
                    //
                  z_motor_bracket_orient() union() {
                    translate([clamp_length / 2 - eta, 0, clamp_height / 2 + eta])
                        cube([clamp_length, clamp_width, clamp_height], center = true);
                    translate([0, 0, clamp_height / 2 + eta])
                        cylinder(h = clamp_height, r = Z_bar_dia/2 + clamp_thickness, center = true);
                  }
                }
                //
                // front corners rounded
                //
                translate([-length / 2, - length / 2, thickness / 2])
                    fillet(r = corner_rad, h = thickness + 1);
                translate([ length / 2, - length / 2, thickness / 2])
                    rotate([0,0, 90])
                        fillet(r = corner_rad, h = thickness + 1);
                //
                // Cut out between webs
                //
                translate([0, length / 2 + cutout / 2 - eta, 0])
                    rounded_rectangle([length - 4 * z_slot_inset - 2 * thickness, cutout, back_height * 2 + 1], r = corner_rad / 2, center = true);
                //
                // motor holes
                //
                poly_cylinder(r = big_hole, h = thickness * 2 + 1, center = true);                   // hole for stepper locating boss

                for(x = NEMA_holes(Z_motor))                                                         // motor screw holes
                    for(y = NEMA_holes(Z_motor))
                        translate([x,y,0])
                            poly_cylinder(r = M3_clearance_radius, h = 2 * thickness + 1, center = true);
                //
                // bar clamp
                //
                z_motor_bracket_orient() union() {
                translate([clamp_length / 2, 0, 0])                            // clamp slot
                    cube([clamp_length, gap,  clamp_height * 2 + 1], center = true);

                translate([clamp_x, Z_bar_dia / 2 + clamp_thickness, clamp_height / 2])
                    rotate([90, 0, 0])
                        nut_trap(screw_clearance_radius, nut_radius, nut_trap_depth, horizontal = true);  // clamp screw

                translate([0, 0,  0])
                    poly_cylinder(r = Z_bar_dia / 2, h = clamp_height * 2 + 1, center = true);       // hole for z rod
                }

                //
                // screw slots in the back
                //
                for(side = [-1, 1])
                    translate([side * (length / 2 - z_slot_inset + z_nut_offset), width - length / 2 - back_thickness,  back_height / 2 + thickness / 2])
                        rotate([90, 0, 0])
                            if(frame_nut_traps)
                                nut_trap(screw_clearance_radius(frame_screw), nut_radius(frame_nut), back_thickness - part_base_thickness, true);
                            else
                                vertical_tearslot(h = back_thickness * 2 + 1, l = back_height - thickness - 2 * z_slot_inset,
                                    r = screw_clearance_radius(frame_screw), center = true);
                //
                // rounded corners on the back
                //
                translate([-length / 2, width - length / 2 - back_thickness / 2, back_height])
                    rotate([-90, 0, 0])
                        fillet(r = corner_rad, h = back_thickness + 1);

                translate([length / 2, width - length / 2 - back_thickness / 2, back_height])
                    rotate([-90, 90, 0])
                        fillet(r = corner_rad, h = back_thickness + 1);
            }
        }
}

module z_motor_bracket_hole_positions(gantry_setback)
    for(side = [-1, 1])
        translate([side * z_motor_bracket_hole_offset(), gantry_setback - part_base_thickness,  back_height / 2 + thickness / 2])
            rotate([90, 0, 0])
                child();

module z_motor_bracket_holes(gantry_setback)
    z_motor_bracket_hole_positions(gantry_setback)
        if(frame_nut_traps)
            rotate([0, 0, 90])
                slot(h = 100, l = back_height - thickness - 2 * z_slot_inset, r = screw_clearance_radius(frame_screw), center = true);
        else
            frame_screw_hole();


module z_motor_assembly(gantry_setback, rhs, rotated = true) {
    assembly("z_motor_assembly");

    color(z_motor_bracket_color) render() z_motor_bracket(gantry_setback, rhs);


    z_motor_bracket_orient() union() {
    //
    // Clamp screw and washer
    //
    translate([clamp_x, -clamp_width / 2, clamp_height / 2])
        rotate([90, 0, 0])
            screw_and_washer(cap_screw, screw_longer_than(clamp_width + washer_thickness(screw_washer(cap_screw))));
    //
    // Clamp nyloc
    //
    translate([clamp_x, clamp_width / 2 - nut_trap_depth, clamp_height / 2])
        rotate([-90, 0, 0])
            nut(nut, true);
    }

    //
    // Mounting screws
    //
    z_motor_bracket_hole_positions(gantry_setback)
        frame_screw(part_base_thickness);
    //
    // Motor and screws
    //
    NEMA(Z_motor);
    translate([0,0, thickness])
        NEMA_screws(Z_motor);

    //
    // The coupling assembly
    //
    explode([0, 0, 30])
        translate([0, 0, NEMA_shaft_length(Z_motor)])
            rotate([0, 0, rotated ? 45 : 0])
                z_coupler_assembly();

   end("z_motor_assembly");

}

module z_motor_bracket_lhs_stl()                 z_motor_bracket(gantry_setback, false);
module z_motor_bracket_rhs_stl() mirror([1,0,0]) z_motor_bracket(gantry_setback, true);

module z_motor_brackets_stl() {
    translate([ length / 2 + 1, 0, 0]) z_motor_bracket_lhs_stl();
    translate([-length / 2 - 1, 0, 0]) z_motor_bracket_rhs_stl();
}

module z_motor_bracketsX2_stl() {
    translate([0, -gantry_setback - 1, 0])
        z_motor_brackets_stl();
    rotate([0, 0, 180])
        translate([0, -gantry_setback - 1, 0])
            z_motor_brackets_stl();

}

if(0)
    if(1)
        z_motor_brackets_stl();
    else
        z_motor_bracketsX2_stl();
else
    z_motor_assembly(gantry_setback, false);

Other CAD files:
alaska90/stls/z_motor_bracket_rhs.stl
alaska90/sheets/frame_gantry.dxf
alaska90/stls/printed/cal.stl
alaska90/stls/spool_bracket_female.stl
scad/conf/lawlor90_config.scad
alaska90/sheets/frame_base_dxf.scad
alaska90/sheets/frame_gantry_and_y_carriage.dxf
alaska90/sheets/frame_gantry_and_y_carriage_dxf.scad
alaska90/sheets/frame_gantry_dxf.scad
alaska90/sheets/frame_left.dxf
alaska90/sheets/frame_left_dxf.scad
alaska90/sheets/frame_right.dxf
alaska90/sheets/frame_right_dxf.scad
alaska90/sheets/frame_stays_dxf.scad
alaska90/sheets/y_carriage_dxf.scad
alaska90/sheets/y_heatshield_dxf.scad
alaska90/stls/atx_long_bracket.stl
alaska90/stls/atx_short_bracket.stl
alaska90/stls/cable_clip_AB.stl
alaska90/stls/cable_clip_AD.stl
alaska90/stls/cable_clip_CA.stl
alaska90/stls/d_motor_bracket.stl
alaska90/stls/d_motor_bracket_lid.stl
alaska90/stls/d_shell.stl
alaska90/stls/d_shell_lid.stl
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

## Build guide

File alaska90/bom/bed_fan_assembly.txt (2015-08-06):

bed_fan_assembly:
Vitamins:
  4 M4 cap screw x 35mm
  4 Nyloc nut M4
  4 Washer M4 x 9mm x 0.8mm

Printed:
  1 fan_guard.stl

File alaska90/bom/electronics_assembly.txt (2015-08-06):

electronics_assembly:
Vitamins:
  4 M3 cap screw x 25mm
  1 Melzi electronics
  1 Micro SD card
  1 Micro SD to USB adapter
  2 Heatshrink sleeving ID 2.4mm x 15mm
  1 USB A to Mini B lead
  4 Washer M3 x 7mm x 0.5mm
  4 Star washer M3 x 0.5mm

Printed:
  4 pcb_spacer.stl

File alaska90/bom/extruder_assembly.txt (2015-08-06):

extruder_assembly:
Vitamins:
  3 Ball bearing 608 8mm x 22mm x 7mm
  3 M3 cap screw x 16mm
  3 M3 hex screw x 10mm
  2 M4 hex screw x 20mm
  2 M4 hex screw x 50mm
  1 M8 hex screw x 60mm, hobbed at 25
  3 Nut M3
  2 Nut M4
  2 Nut M8
  1 Smooth rod 8mm x 22mm
  2 Spring 7mm OD, 1mm gauge x 10mm long
  3 Washer M3 x 7mm x 0.5mm
  7 Washer M4 x 9mm x 0.8mm
  6 Star washer M3 x 0.5mm
  1 Star washer M8 x 1.6mm

Printed:
  1 wades_big_gear.stl
  1 wades_block.stl
  1 wades_gear_spacer.stl
  1 wades_idler_block.stl

Sub-assemblies:
  1 extruder_motor_assembly

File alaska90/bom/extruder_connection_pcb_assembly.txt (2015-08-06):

extruder_connection_pcb_assembly:
Vitamins:
  1 15 way D PCB mount plug
  1 2 way Molex KK header
  1 3 way Molex KK header
  1 Extruder connection PCB
  2 4 way terminal block

Printed:

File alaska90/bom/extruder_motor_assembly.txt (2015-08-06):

extruder_motor_assembly:
Vitamins:
  2 M3 cap screw x 45mm
  1 M3 grub screw x 6mm
  1 NEMA17 x 48mm stepper motor
  3 Nut M3
  2 No2 pan wood screw x 13mm
  2 Washer M2.5 x 5.9mm x 0.5mm
  2 Washer M3 x 7mm x 0.5mm

Printed:
  1 d_motor_bracket.stl
  1 d_motor_bracket_lid.stl
  1 wades_small_gear.stl

Sub-assemblies:
  1 extruder_connection_pcb_assembly

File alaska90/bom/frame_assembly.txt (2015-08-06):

frame_assembly:
Vitamins:
 39 1/4in hex screw x 25mm
  2 MDF sheet 532mm x 809mm x 19.5mm
  1 MDF sheet 916mm x 1213mm x 19.5mm
  1 MDF sheet 916mm x 809mm x 19.5mm
 39 Washer M8 x 17mm x 1.6mm
 39 Star washer M8 x 1.6mm

Printed:
  2 cable_clip_AB.stl
  2 cable_clip_AD.stl
  1 cable_clip_CA.stl
 10 fixing_block.stl
  1 ribbon_clamp_20_66.stl
  1 ribbon_clamp_26_66.stl

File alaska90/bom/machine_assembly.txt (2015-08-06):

machine_assembly:
Vitamins:

Printed:

Sub-assemblies:
  1 bed_fan_assembly
  1 electronics_assembly
  1 frame_assembly
  1 psu_assembly
  1 spool_holder_assembly
  1 x_axis_assembly
  1 y_axis_assembly
  1 z_axis_assembly

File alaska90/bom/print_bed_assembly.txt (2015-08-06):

print_bed_assembly:
Vitamins:
  4 19mm bulldog clip
  1 PCB bed 615mm x 615mm
  2 Corrugated cardboard 578mm x 618mm x 5mm
  4 M3 cap screw x 10mm
  1 Glass sheet 615mm x 603mm x 2mm
  4 Hex male / female pillar M6.5 x 13mm
  1 Polypropylene strip 466mm x 33mm x 0.5mm
  1 Ribbon cable 26 way 576mm
  2 Heatshrink sleeving ID 1.6mm x 15mm
  2 Heatshrink sleeving ID 2.4mm x 15mm
  2 Heatshrink sleeving ID 6.4mm x 30mm
  1 Epcos B57861S104F40 100K 1% thermistor
  4 Washer M3 x 7mm x 0.5mm
  1 Black wire 32/0.2 length 635mm
  1 Red wire 32/0.2 length 620mm

Printed:

Sub-assemblies:
  1 y_carriage_assembly

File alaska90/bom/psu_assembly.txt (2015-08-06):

psu_assembly:
Vitamins:
  1 THS15 Aluminium clad resistor 10R
  1 THS15 Aluminium clad resistor 4R7
  1 PSU e.g. ALPINE500
  1 IEC mains lead
  4 1/4in hex screw x 25mm
  2 6-32 pan screw x 9.5mm
  4 No2 pan wood screw x 13mm
  1 Heatshrink sleeving ID 10mm x 15mm
  3 Heatshrink sleeving ID 2.4mm x 15mm
  5 Heatshrink sleeving ID 3.2mm x 15mm
  2 Heatshrink sleeving ID 6.4mm x 15mm
  2 Washer M4 x 9mm x 0.8mm
  4 Washer M8 x 17mm x 1.6mm
  2 Star washer M4 x 0.8mm
  4 Star washer M8 x 1.6mm
  2 Ziptie 100mm min length

Printed:
  1 atx_long_bracket.stl
  1 atx_short_bracket.stl

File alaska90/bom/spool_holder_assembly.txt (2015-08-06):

spool_holder_assembly:
Vitamins:
  4 Ball bearing 608 8mm x 22mm x 7mm
  1 Foam sponge 20mm x 20mm x 20mm
  2 1/4in hex screw x 25mm
  1 PLA sample 3mm ~50m
  1 PTFE tubing OD 4.6mm ID 3.84mm x 750mm
 14 Washer M8 x 17mm x 1.6mm
  4 Washer M8 x 30mm x 1.5mm
  2 Star washer M8 x 1.6mm

Printed:
  1 dust_filter.stl
  2 spool_bracket_female.stl
  2 spool_bracket_male.stl

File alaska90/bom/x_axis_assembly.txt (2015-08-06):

x_axis_assembly:
Vitamins:
  1 Belt T5 x 6mm x 1760mm
  2 Smooth rod 16mm x 829mm
  2 Wingnut M4

Printed:

Sub-assemblies:
  1 extruder_assembly
  1 x_carriage_assembly
  1 x_carriage_fan_assembly

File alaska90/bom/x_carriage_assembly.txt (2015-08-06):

x_carriage_assembly:
Vitamins:
  2 M3 cap screw x 10mm
  1 M3 cap screw x 20mm
  2 M3 cap screw x 25mm
  1 LM16UU linear bearing
  1 Nut M3
  4 Nyloc nut M3
  4 Washer M3 x 7mm x 0.5mm
  3 Ziptie 140mm min length

Printed:
  1 x_belt_clamp.stl
  1 x_belt_grip.stl
  1 x_belt_tensioner.stl
  1 x_carriage.stl

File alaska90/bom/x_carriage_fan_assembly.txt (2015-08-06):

x_carriage_fan_assembly:
Vitamins:
  4 M4 cap screw x 30mm
  1 Fan 60mm x 15mm
  4 Nyloc nut M4
  4 Washer M4 x 9mm x 0.8mm

Printed:
  1 x_carriage_fan_bracket.stl
  1 x_carriage_fan_duct.stl

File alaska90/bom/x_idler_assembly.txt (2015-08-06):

x_idler_assembly:
Vitamins:
  2 Ball bearing 624 4mm x 13mm x 5mm
  8 M3 cap screw x 30mm
  1 M4 cap screw x 45mm
  2 LM16UU linear bearing
  8 Nyloc nut M3
  1 Nyloc nut M4
  8 Washer M3 x 7mm x 0.5mm
  2 Washer M4 x 9mm x 0.8mm
  2 Washer M5 x 20mm x 1.4mm

Printed:
  2 x_end_clamp.stl
  1 x_idler_bracket.stl

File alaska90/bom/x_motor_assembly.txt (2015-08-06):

x_motor_assembly:
Vitamins:
  6 M3 cap screw x 16mm
  2 M3 cap screw x 20mm
  8 M3 cap screw x 30mm
  1 M3 cap screw x 45mm
  1 15 way D IDC socket
  1 M3 grub screw x 6mm
  2 LM16UU linear bearing
  1 NEMA17 x 48mm stepper motor
  1 Nut M3
 14 Nyloc nut M3
  2 Nitrile O-ring 2.5mm x 1.6mm
  1 Polypropylene strip 793mm x 18mm x 0.5mm
  1 Polypropylene strip 984mm x 25mm x 0.5mm
  2 M3 pan screw x 8mm
  4 No2 pan wood screw x 13mm
  1 Ribbon cable 20 way 2147mm
  1 Microswitch
  4 Heatshrink sleeving ID 2.4mm x 15mm
  4 Washer M2.5 x 5.9mm x 0.5mm
 21 Washer M3 x 7mm x 0.5mm
  2 Star washer M3 x 0.5mm

Printed:
  1 d_shell.stl
  1 d_shell_lid.stl
  1 pulley.stl
  1 ribbon_clamp_14_33.stl
  1 ribbon_clamp_14_33NB.stl
  1 ribbon_clamp_20_33.stl
  2 x_end_clamp.stl
  1 x_motor_bracket.stl
  1 x_motor_ribbon_bracket.stl

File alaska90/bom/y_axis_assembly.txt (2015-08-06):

y_axis_assembly:
Vitamins:
  1 Belt T5 x 6mm x 1820mm
 12 1/4in hex screw x 25mm
  4 Nyloc nut M6.4
  2 No2 pan wood screw x 13mm
  1 Smooth rod 16mm x 1209mm
  1 Smooth rod 16mm x 692mm
  1 Microswitch
  2 Washer M2.5 x 5.9mm x 0.5mm
 12 Washer M8 x 17mm x 1.6mm
  8 Star washer M8 x 1.6mm

Printed:
  3 y_bar_clamp.stl
  1 y_bar_clamp_switch.stl

Sub-assemblies:
  1 print_bed_assembly
  1 y_idler_assembly
  1 y_motor_assembly

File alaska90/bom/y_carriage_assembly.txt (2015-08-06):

y_carriage_assembly:
Vitamins:
  8 M3 cap screw x 16mm
  6 1/4in hex screw x 16mm
  2 1/4in hex screw x 20mm
  3 LM16UU linear bearing
  1 MDF sheet 618mm x 618mm x 10mm
  8 Nyloc nut M3
  8 Nyloc nut M6.4
  8 Washer M3 x 7mm x 0.5mm
 14 Washer M8 x 17mm x 1.6mm
  3 Ziptie 140mm min length

Printed:
  1 ribbon_clamp_26_66.stl
  1 ribbon_clamp_26_66N.stl
  3 y_bearing_mount.stl
  1 y_belt_anchor.stl
  1 y_belt_anchor_toothed.stl
  1 y_belt_clip.stl
  1 y_belt_clip_toothed.stl

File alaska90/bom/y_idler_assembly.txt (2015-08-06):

y_idler_assembly:
Vitamins:
  2 Ball bearing 624 4mm x 13mm x 5mm
  1 M4 cap screw x 30mm
  1 1/4in hex screw x 25mm
  1 Nyloc nut M4
  4 Washer M4 x 9mm x 0.8mm
  2 Washer M5 x 20mm x 1.4mm
  1 Washer M8 x 17mm x 1.6mm
  1 Star washer M8 x 1.6mm

Printed:
  1 y_idler_bracket.stl

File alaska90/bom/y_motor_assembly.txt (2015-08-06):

y_motor_assembly:
Vitamins:
  1 M3 grub screw x 6mm
  4 1/4in hex screw x 25mm
  1 NEMA17 x 48mm stepper motor
  1 Nut M3
  4 M3 pan screw x 8mm
  4 Washer M3 x 7mm x 0.5mm
  4 Washer M8 x 17mm x 1.6mm
  4 Star washer M3 x 0.5mm
  4 Star washer M8 x 1.6mm

Printed:
  1 pulley.stl
  1 y_motor_bracket.stl

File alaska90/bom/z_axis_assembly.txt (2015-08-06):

z_axis_assembly:
Vitamins:
  6 1/4in hex screw x 25mm
  2 Brass nut M8
  2 Nyloc nut M6.4
  2 Smooth rod 16mm x 759mm
  2 Threaded rod M9.5 x 711mm
  6 Washer M8 x 17mm x 1.6mm
  4 Star washer M8 x 1.6mm

Printed:
  2 z_bar_clamp.stl
  2 z_screw_pointer.stl

Sub-assemblies:
  1 x_idler_assembly
  1 x_motor_assembly
  1 z_limit_switch_assembly
  2 z_motor_assemblies

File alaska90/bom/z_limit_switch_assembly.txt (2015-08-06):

z_limit_switch_assembly:
Vitamins:
  1 M3 hex screw x 16mm
  2 1/4in hex screw x 25mm
  1 Nyloc nut M3
  2 No2 pan wood screw x 13mm
  1 Microswitch
  2 Washer M2.5 x 5.9mm x 0.5mm
  1 Washer M3 x 7mm x 0.5mm
  2 Washer M8 x 17mm x 1.6mm
  2 Rubber washer M3 x 10mm x 1.5mm
  2 Star washer M8 x 1.6mm

Printed:
  1 z_limit_switch_bracket.stl

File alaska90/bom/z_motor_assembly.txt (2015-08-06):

z_motor_assemblies:
Vitamins:
  8 M3 cap screw x 20mm
  6 1/4in hex screw x 25mm
  2 NEMA17 x 48mm stepper motor
  8 Nyloc nut M3
  2 Nyloc nut M6.4
  8 M3 pan screw x 8mm
  2 Neoprene tubing OD 8mm ID 5mm x 16mm
 16 Washer M3 x 7mm x 0.5mm
  6 Washer M8 x 17mm x 1.6mm
  8 Star washer M3 x 0.5mm
  4 Star washer M8 x 1.6mm

Printed:
  4 z_coupling.stl
  1 z_motor_bracket_lhs.stl
  1 z_motor_bracket_rhs.stl

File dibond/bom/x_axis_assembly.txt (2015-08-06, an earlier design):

x_axis_assembly:
Vitamins:
  1 Belt T2 x 6mm x 860mm
  2 Smooth rod 8mm x 381mm
  2 Wingnut M4

Printed:

Sub-assemblies:
  1 extruder_assembly
  1 x_carriage_assembly
  1 x_carriage_fan_assembly

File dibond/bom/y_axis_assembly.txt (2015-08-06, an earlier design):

y_axis_assembly:
Vitamins:
  1 Belt T2 x 6mm x 662mm
  4 M3 cap screw x 16mm
  8 M4 cap screw x 16mm
  4 Nyloc nut M3
  8 Nyloc nut M4
  2 No2 pan wood screw x 13mm
  1 Smooth rod 8mm x 270mm
  1 Smooth rod 8mm x 417mm
  1 Microswitch
  2 Washer M2.5 x 5.9mm x 0.5mm
  4 Washer M3 x 7mm x 0.5mm
  8 Washer M4 x 9mm x 0.8mm

Printed:
  3 y_bar_clamp.stl
  1 y_bar_clamp_switch.stl

Sub-assemblies:
  1 print_bed_assembly
  1 y_idler_assembly
  1 y_motor_assembly

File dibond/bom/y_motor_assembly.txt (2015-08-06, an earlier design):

y_motor_assembly:
Vitamins:
  4 M4 cap screw x 16mm
  2 M3 grub screw x 6mm
  1 NEMA17 x 47mm stepper motor
  4 Nyloc nut M4
  4 M3 pan screw x 8mm
  1 GT2 pulley 20 teeth
  4 Washer M3 x 7mm x 0.5mm
  4 Washer M4 x 9mm x 0.8mm
  4 Star washer M3 x 0.5mm

Printed:
  1 y_motor_bracket.stl

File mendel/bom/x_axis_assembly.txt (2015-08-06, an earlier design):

x_axis_assembly:
Vitamins:
  1 Belt T2 x 6mm x 868mm
  2 Smooth rod 8mm x 385mm
  2 Wingnut M4

Printed:

Sub-assemblies:
  1 extruder_assembly
  1 x_carriage_assembly
  1 x_carriage_fan_assembly

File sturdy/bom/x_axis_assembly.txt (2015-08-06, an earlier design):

x_axis_assembly:
Vitamins:
  1 Belt T2 x 6mm x 904mm
  2 Smooth rod 10mm x 403mm
  2 Wingnut M4

Printed:

Sub-assemblies:
  1 extruder_assembly
  1 x_carriage_assembly
  1 x_carriage_fan_assembly

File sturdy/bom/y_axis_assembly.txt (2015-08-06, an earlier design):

y_axis_assembly:
Vitamins:
  1 Belt T2 x 6mm x 680mm
  4 M4 cap screw x 20mm
  4 Nyloc nut M4
  2 No2 pan wood screw x 13mm
  8 No6 pan wood screw x 16mm
  1 Smooth rod 10mm x 290mm
  1 Smooth rod 10mm x 432mm
  1 Microswitch
  2 Washer M2.5 x 5.9mm x 0.5mm
 12 Washer M4 x 9mm x 0.8mm
  8 Star washer M4 x 0.8mm

Printed:
  3 y_bar_clamp.stl
  1 y_bar_clamp_switch.stl

Sub-assemblies:
  1 print_bed_assembly
  1 y_idler_assembly
  1 y_motor_assembly

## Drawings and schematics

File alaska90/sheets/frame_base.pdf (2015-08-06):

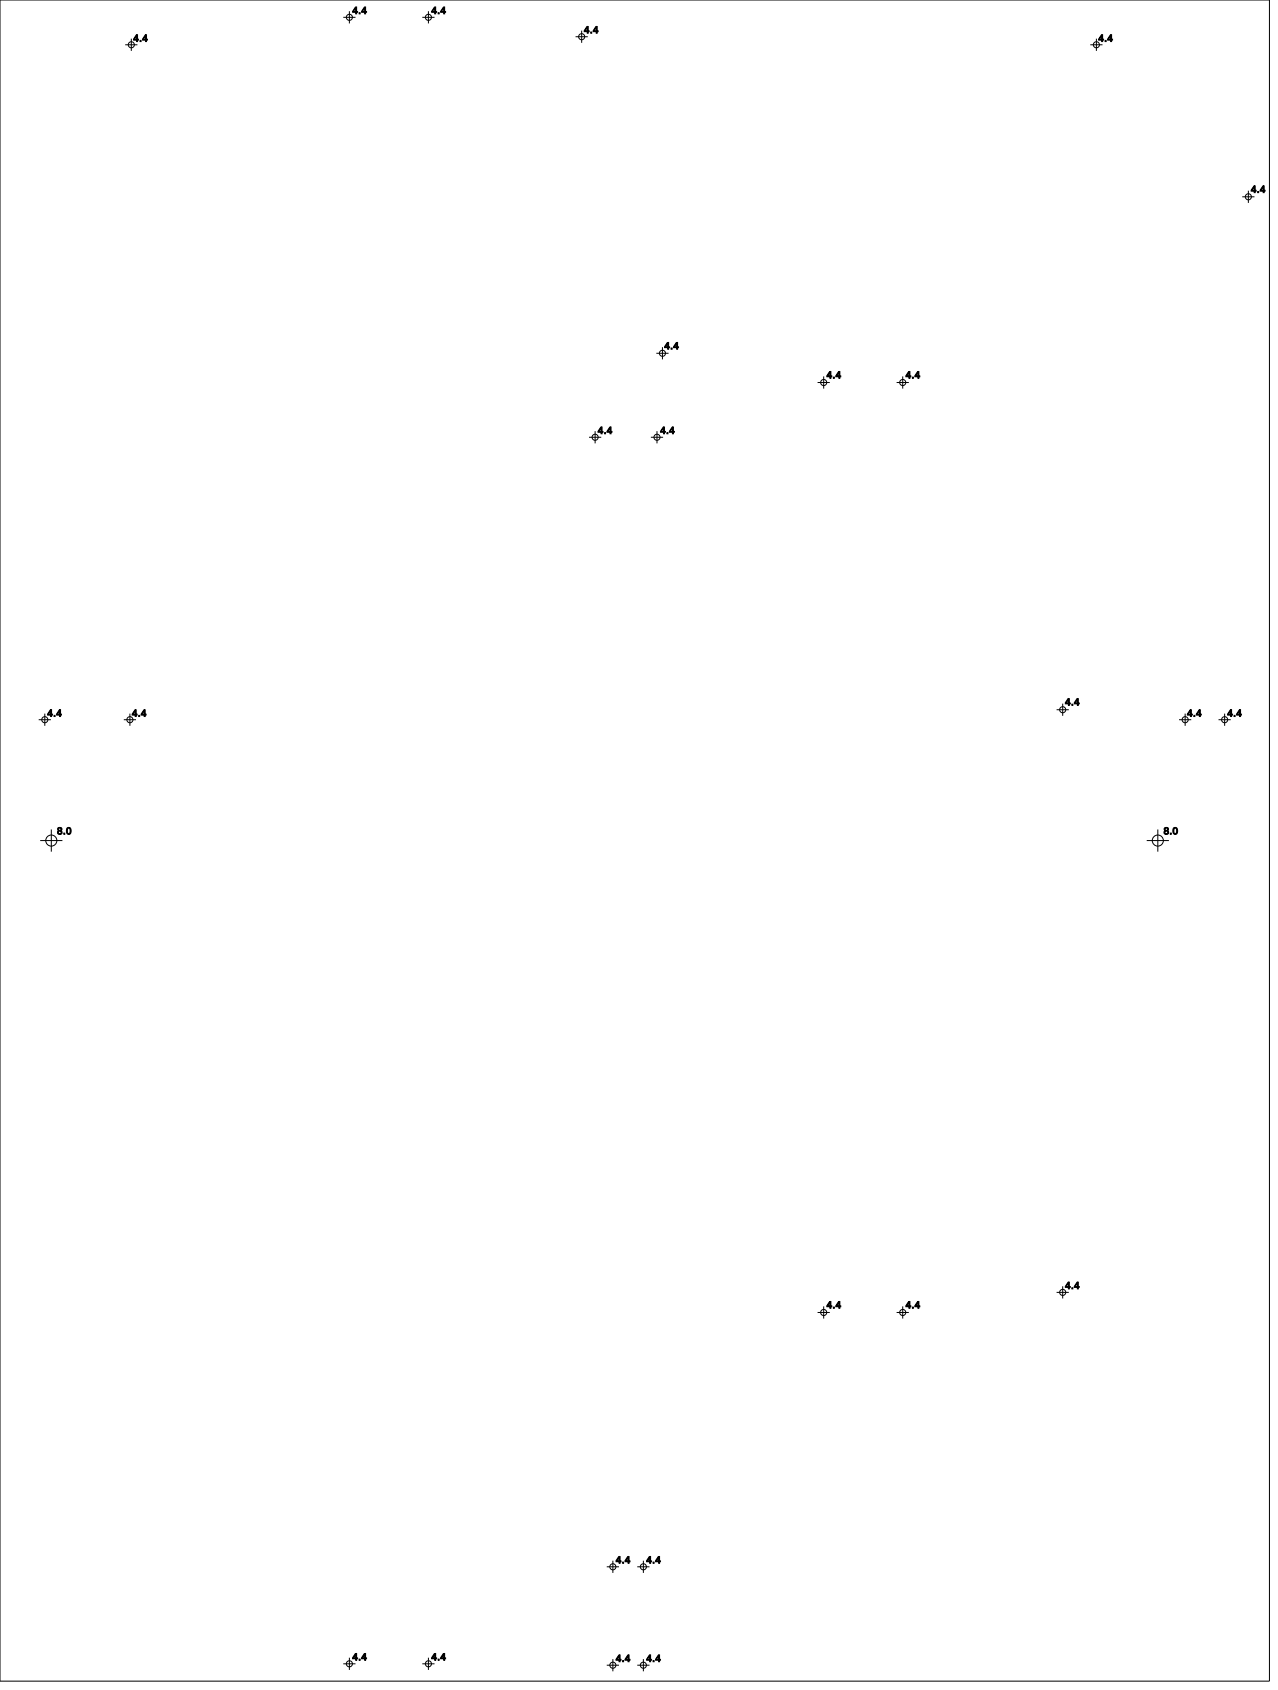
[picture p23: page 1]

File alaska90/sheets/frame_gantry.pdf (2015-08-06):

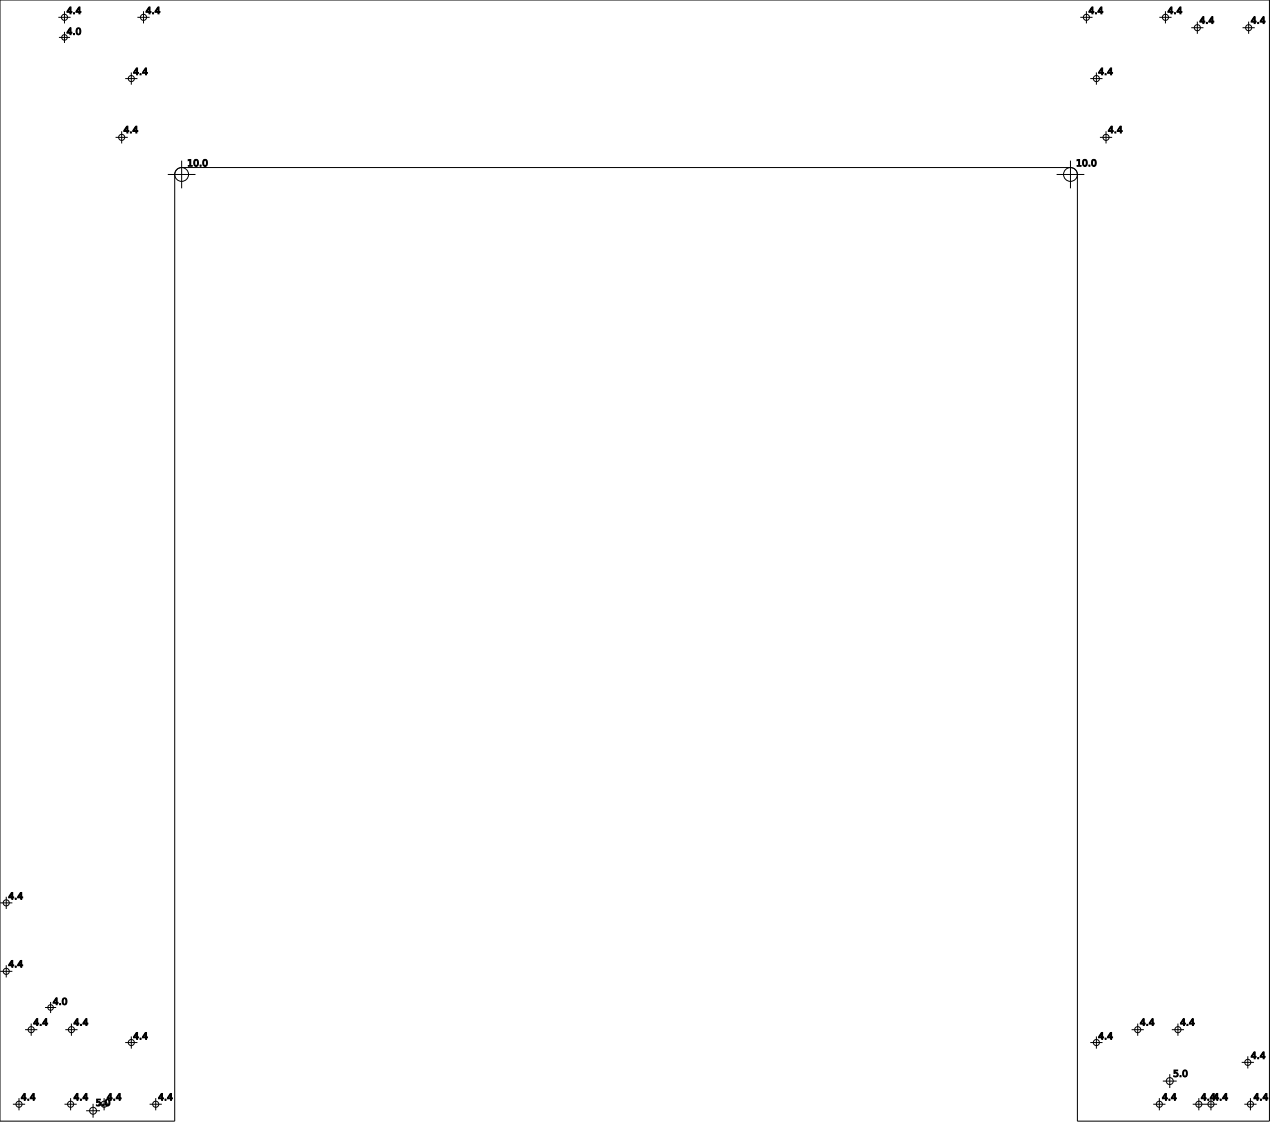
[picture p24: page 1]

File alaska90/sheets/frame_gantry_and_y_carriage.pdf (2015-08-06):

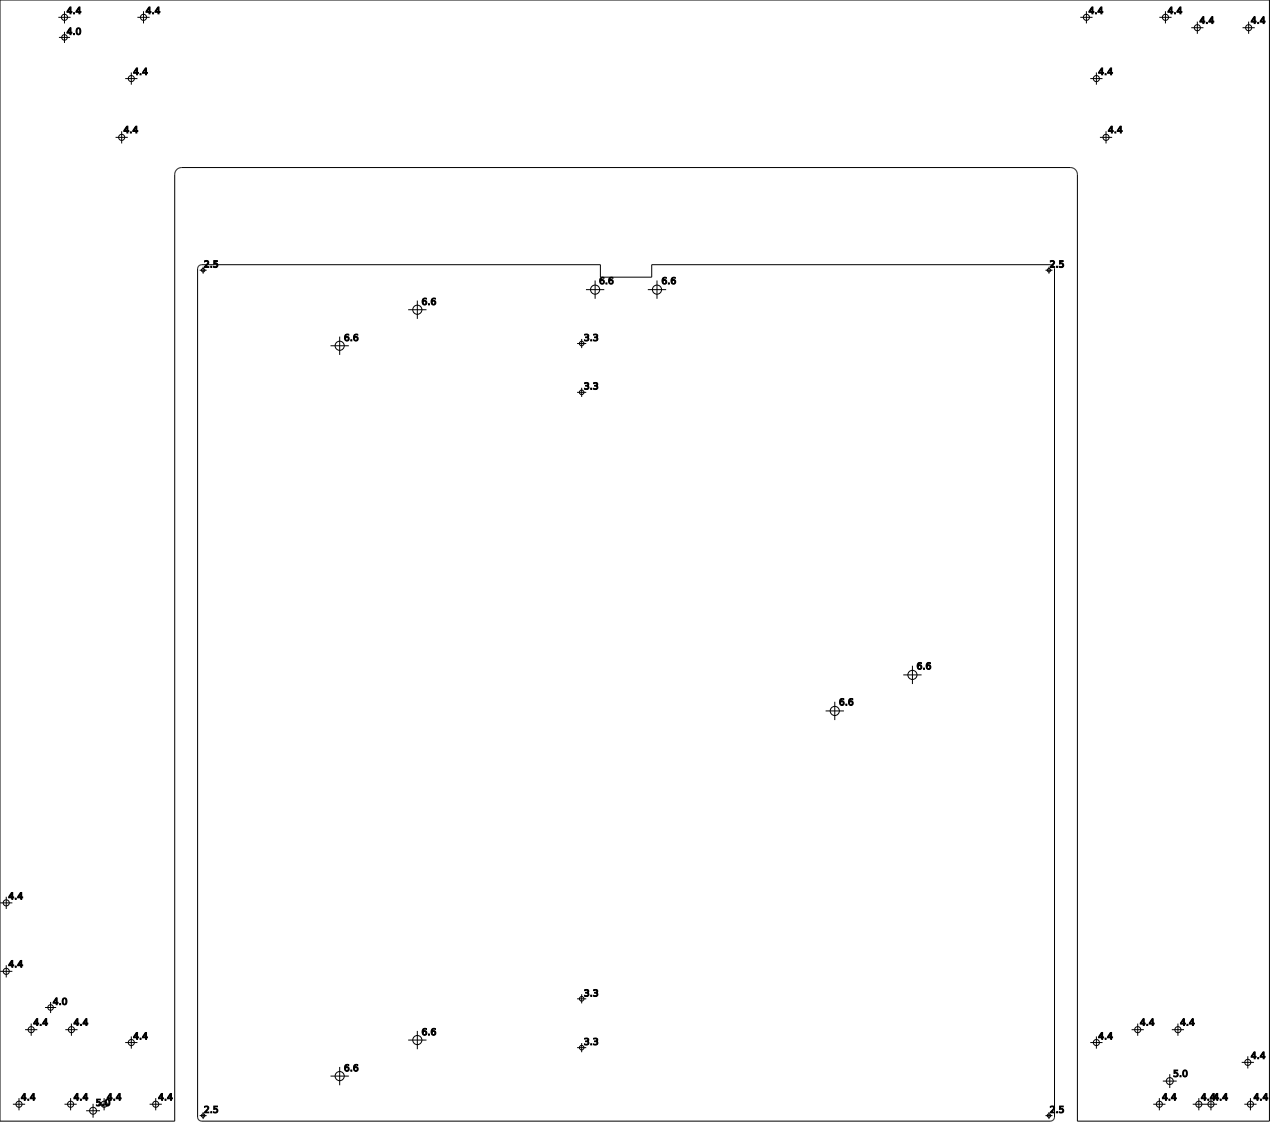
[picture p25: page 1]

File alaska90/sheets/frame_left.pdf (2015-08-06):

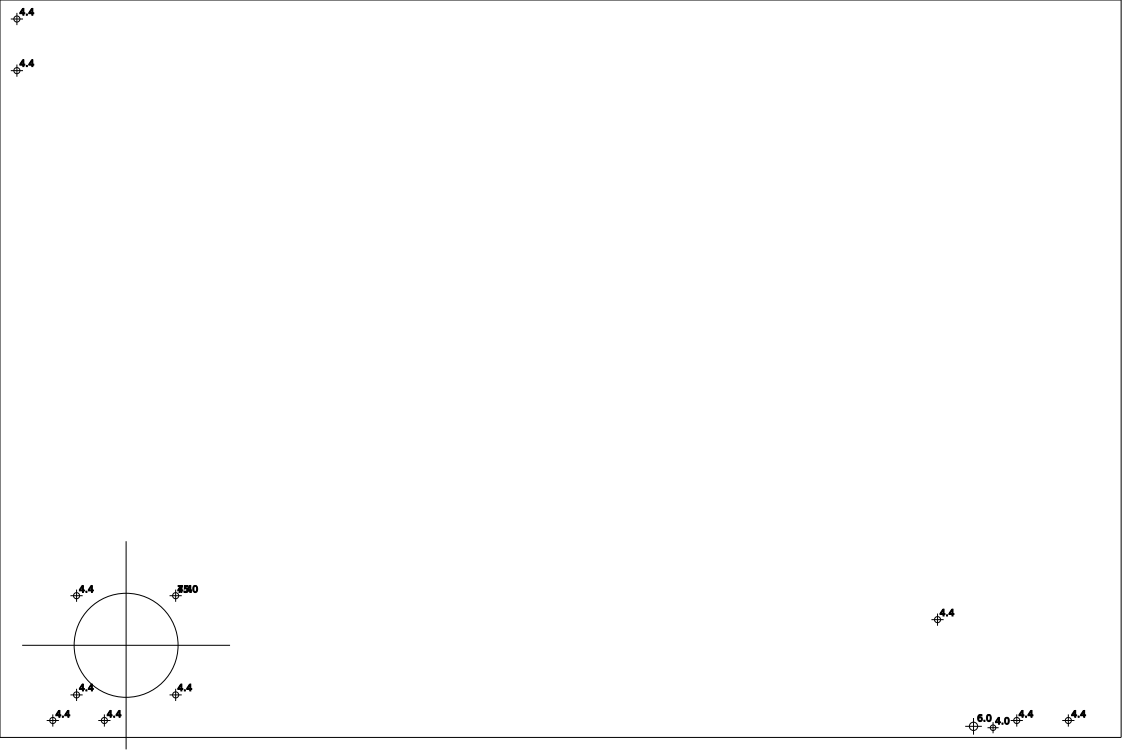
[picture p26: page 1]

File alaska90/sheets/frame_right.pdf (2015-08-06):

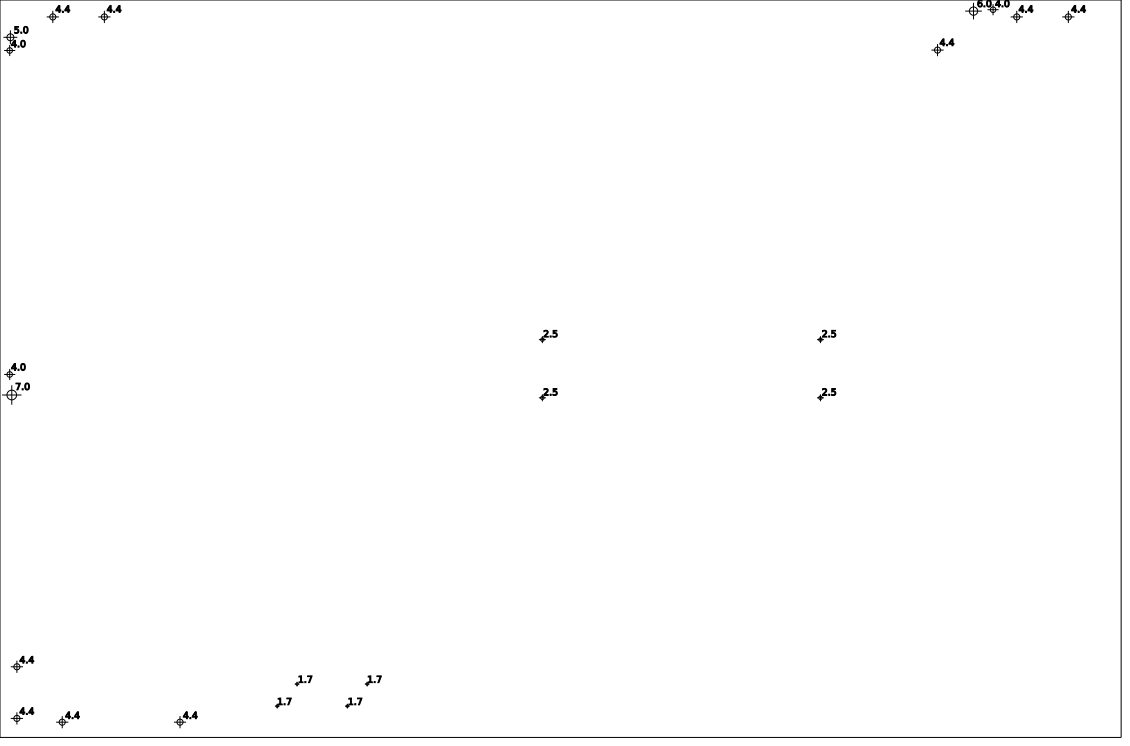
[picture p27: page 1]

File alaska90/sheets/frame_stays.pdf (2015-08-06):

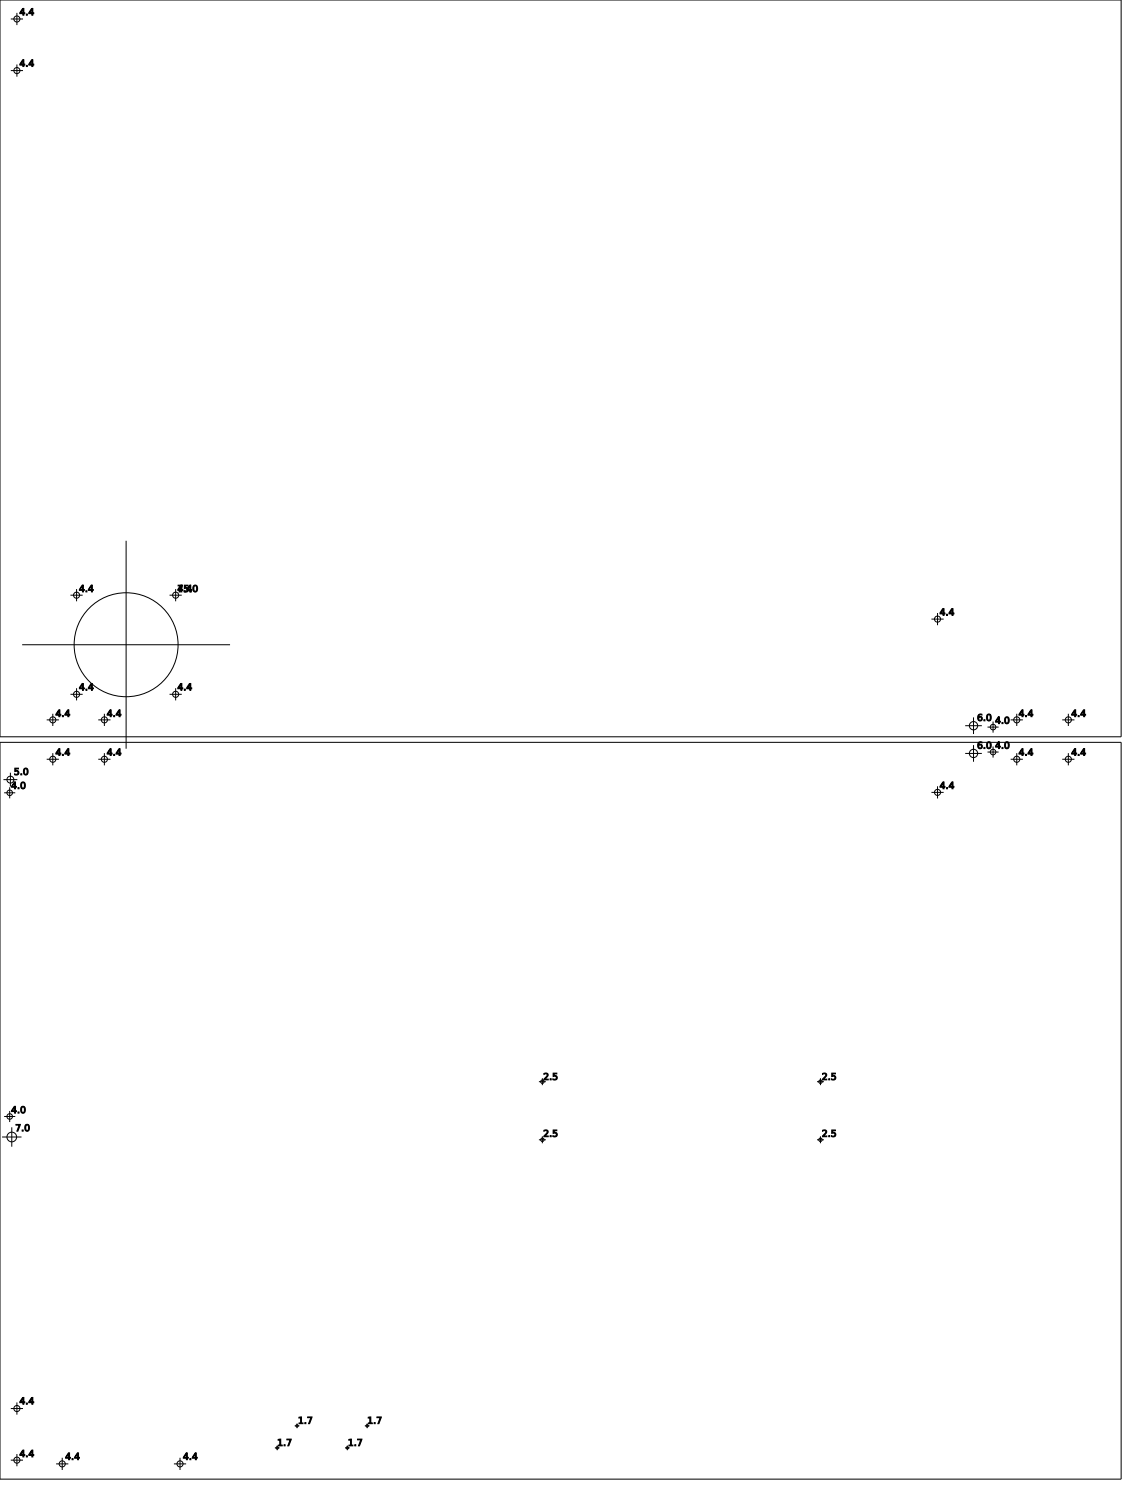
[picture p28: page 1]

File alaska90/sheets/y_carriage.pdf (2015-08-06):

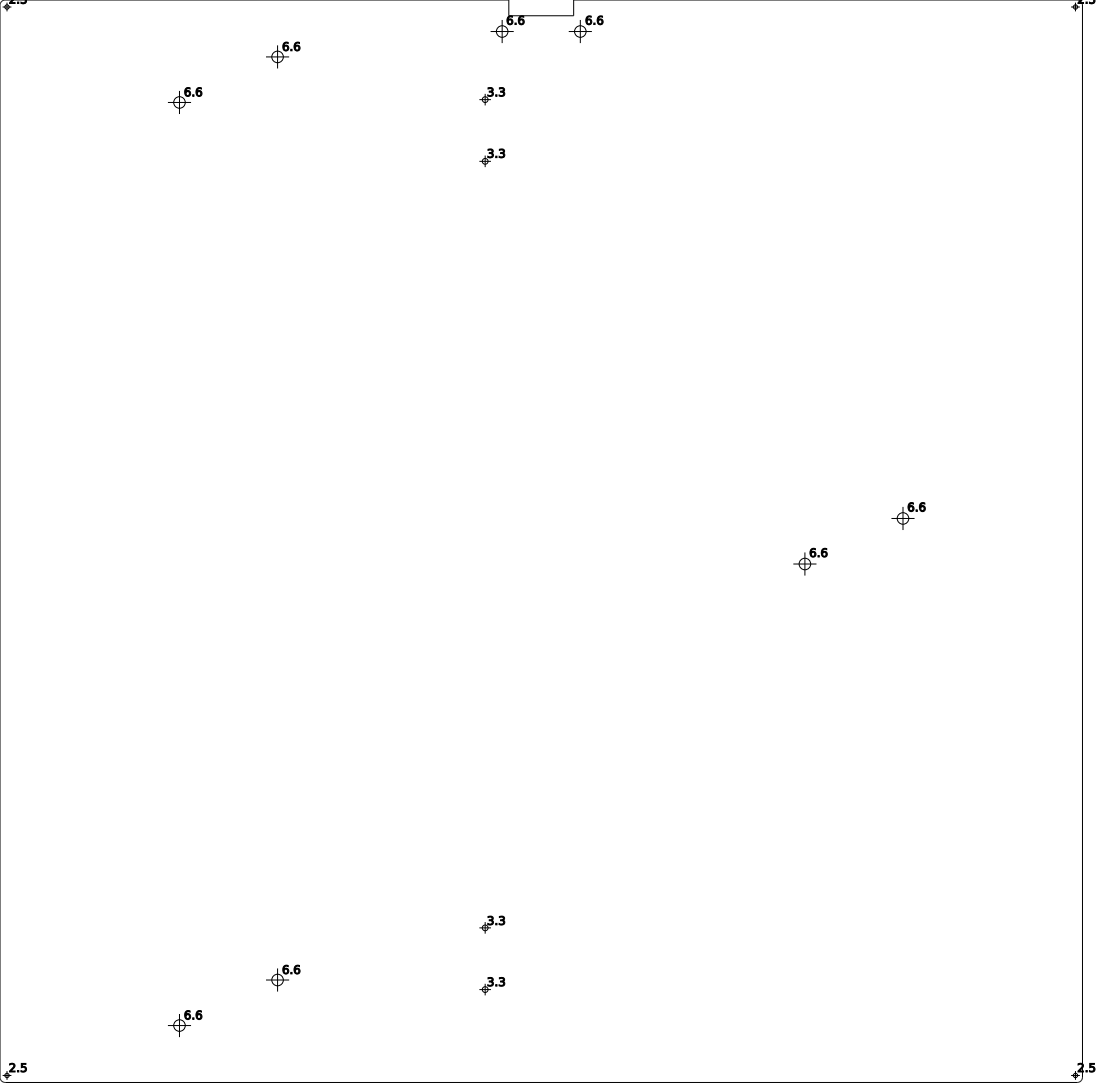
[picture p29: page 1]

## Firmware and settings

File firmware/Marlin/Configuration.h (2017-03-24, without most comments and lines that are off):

#define CONFIGURATION_H
#define STRING_VERSION_CONFIG_H __DATE__ " " __TIME__ // build date and time
#define STRING_CONFIG_H_AUTHOR "(Dr. Orion Lawlor, 2017-03-16)" // Who made the changes.
#define SERIAL_PORT 0
#define BAUDRATE 115200  //  OSL: was  250000
#define MOTHERBOARD 63
#define CUSTOM_MENDEL_NAME "Alaska90"
#define EXTRUDERS 3
#define POWER_SUPPLY 1
#define TEMP_SENSOR_0 1
#define TEMP_SENSOR_1 1
#define TEMP_SENSOR_2 1
#define TEMP_SENSOR_BED 1
#define MAX_REDUNDANT_TEMP_SENSOR_DIFF 10
#define TEMP_RESIDENCY_TIME 10  // (seconds)
#define TEMP_HYSTERESIS 3       // (degC) range of +/- temperatures considered "close" to the target one
#define TEMP_WINDOW     1       // (degC) Window around target to start the residency timer x degC early.
#define HEATER_0_MINTEMP 3
#define HEATER_1_MINTEMP 3
#define HEATER_2_MINTEMP 3
#define BED_MINTEMP 3
#define HEATER_0_MAXTEMP 260
#define HEATER_1_MAXTEMP 260
#define HEATER_2_MAXTEMP 260
#define BED_MAXTEMP 120
#define PIDTEMP
#define BANG_MAX 255 // limits current to nozzle while in bang-bang mode; 255=full current
#define PID_MAX 255 // limits current to nozzle while PID is active (see PID_FUNCTIONAL_RANGE below); 255=full current
  #define PID_FUNCTIONAL_RANGE 10 // If the temperature difference between the target temperature and the actual temperature
  #define PID_INTEGRAL_DRIVE_MAX 255  //limit for the integral term
  #define K1 0.95 //smoothing factor within the PID
  #define PID_dT ((OVERSAMPLENR * 10.0)/(F_CPU / 64.0 / 256.0)) //sampling period of the temperature routine
    #define  DEFAULT_Kp 10.2
    #define  DEFAULT_Ki 0.63
    #define  DEFAULT_Kd 40
#define PIDTEMPBED
#define MAX_BED_POWER 255 // limits duty cycle to bed; 255=full current
    #define  DEFAULT_bedKp 46.14
    #define  DEFAULT_bedKi 0.28
    #define  DEFAULT_bedKd 1912.44
#define PREVENT_LENGTHY_EXTRUDE
#define EXTRUDE_MINTEMP 150
#define EXTRUDE_MAXLENGTH (X_MAX_LENGTH+Y_MAX_LENGTH) //prevent extrusion of very large distances.
#define THERMAL_RUNAWAY_PROTECTION_PERIOD 120 //in seconds
#define THERMAL_RUNAWAY_PROTECTION_HYSTERESIS 40 // in degree Celsius
#define THERMAL_RUNAWAY_PROTECTION_BED_PERIOD 120 //in seconds
#define THERMAL_RUNAWAY_PROTECTION_BED_HYSTERESIS 40 // in degree Celsius
#define ENDSTOPPULLUPS // Comment this out (using // at the start of the line) to disable the endstop pullup resistors
  #define ENDSTOPPULLUP_XMAX
  #define ENDSTOPPULLUP_YMAX
  #define ENDSTOPPULLUP_ZMAX
  #define ENDSTOPPULLUP_XMIN
  #define ENDSTOPPULLUP_YMIN
  #define ENDSTOPPULLUP_ZMIN
const bool X_MIN_ENDSTOP_INVERTING = true; // set to true to invert the logic of the endstop.
const bool Y_MIN_ENDSTOP_INVERTING = true; // set to true to invert the logic of the endstop.
const bool Z_MIN_ENDSTOP_INVERTING = true; // set to true to invert the logic of the endstop.
const bool X_MAX_ENDSTOP_INVERTING = true; // set to true to invert the logic of the endstop.
const bool Y_MAX_ENDSTOP_INVERTING = true; // set to true to invert the logic of the endstop.
const bool Z_MAX_ENDSTOP_INVERTING = true; // set to true to invert the logic of the endstop.
#if defined(COREXY) && !defined(DISABLE_MAX_ENDSTOPS)
  #define DISABLE_MAX_ENDSTOPS
#endif
#define X_ENABLE_ON 0
#define Y_ENABLE_ON 0
#define Z_ENABLE_ON 0
#define E_ENABLE_ON 0 // For all extruders
#define DISABLE_X false
#define DISABLE_Y false
#define DISABLE_Z false
#define DISABLE_E false // For all extruders
#define DISABLE_INACTIVE_EXTRUDER false //disable only inactive extruders and keep active extruder enabled
#define INVERT_X_DIR false    // Alaska90
#define INVERT_Y_DIR false    // Alaska90
#define INVERT_Z_DIR false     // Alaska90
#define INVERT_E0_DIR false   // for direct drive extruder v9 set to true, for geared extruder set to false
#define INVERT_E1_DIR false    // for direct drive extruder v9 set to true, for geared extruder set to false
#define INVERT_E2_DIR false   // for direct drive extruder v9 set to true, for geared extruder set to false
#define X_HOME_DIR 1
#define Y_HOME_DIR 1
#define Z_HOME_DIR -1
#define min_software_endstops true // If true, axis won't move to coordinates less than HOME_POS.
#define max_software_endstops true  // If true, axis won't move to coordinates greater than the defined lengths below.
#define X_MAX_POS 578  // 600 is full travel (minus fan)
#define X_MIN_POS 0
#define Y_MAX_POS 508  // 510 is full travel
#define Y_MIN_POS 0
#define Z_MAX_POS 450  // 450 starts to hit spool; 620 is about full
#define Z_MIN_POS 0
#define X_MAX_LENGTH (X_MAX_POS - X_MIN_POS)
#define Y_MAX_LENGTH (Y_MAX_POS - Y_MIN_POS)
#define Z_MAX_LENGTH (Z_MAX_POS - Z_MIN_POS)
#define Z_PROBE_REPEATABILITY_TEST  // If not commented out, Z-Probe Repeatability test will be included if Auto Bed Leveling is Enabled.
#define MANUAL_X_HOME_POS 0
#define MANUAL_Y_HOME_POS 0
#define MANUAL_Z_HOME_POS 0
#define NUM_AXIS 4 // The axis order in all axis related arrays is X, Y, Z, E
#define HOMING_FEEDRATE {50*60, 50*60, 4*60, 0}  // set the homing speeds (mm/min)
#define DEFAULT_AXIS_STEPS_PER_UNIT   {80*8/12.0,80*8/12.0,200.0*16/2.1167,((200 * 16 * 39.0)/(11.0 * 7.4 * 3.142)) / 0.94, 600, 600}  // default steps per unit for Alaska90
#define DEFAULT_MAX_FEEDRATE          { 500, 500, 8, 100, 200, 200}    // (mm/sec), conservative numbers
#define DEFAULT_MAX_ACCELERATION      {3000, 500,100,5000,5000,5000}    // (mm/sec^2) start acceleration.   X, Y, Z, E maximum start speed for accelerated moves. E default values are good for Skeinforge 40+, for older versions raise them a lot.
#define DEFAULT_ACCELERATION          3000    // X, Y, Z and E max acceleration in mm/s^2 for printing moves
#define DEFAULT_RETRACT_ACCELERATION  3000   // X, Y, Z and E max acceleration in mm/s^2 for retracts
#define EXTRUDER_OFFSET_X {0.0, -34.00, 2.0} // (in mm) for each extruder, offset of the hotend on the X axis
#define EXTRUDER_OFFSET_Y {0.0, -94.3, -89.3}  // (in mm) for each extruder, offset of the hotend on the Y axis
#define DEFAULT_XYJERK                5.0    // (mm/sec)
#define DEFAULT_ZJERK                 0.4     // (mm/sec)
#define DEFAULT_EJERK                 3.0    // (mm/sec)
#define CUSTOM_M_CODES
  #define CUSTOM_M_CODE_SET_Z_PROBE_OFFSET 851
  #define Z_PROBE_OFFSET_RANGE_MIN -15
  #define Z_PROBE_OFFSET_RANGE_MAX -5
#define PLA_PREHEAT_HOTEND_TEMP 180
#define PLA_PREHEAT_HPB_TEMP 0
#define PLA_PREHEAT_FAN_SPEED 255   // Insert Value between 0 and 255
#define ABS_PREHEAT_HOTEND_TEMP 230
#define ABS_PREHEAT_HPB_TEMP 100
#define ABS_PREHEAT_FAN_SPEED 255   // Insert Value between 0 and 255
#define SDSUPPORT // Enable SD Card Support in Hardware Console
#define SD_CHECK_AND_RETRY // Use CRC checks and retries on the SD communication
#define SOFT_PWM_SCALE 0
#define FILAMENT_SENSOR_EXTRUDER_NUM	0  //The number of the extruder that has the filament sensor (0,1,2)
#define MEASUREMENT_DELAY_CM			14  //measurement delay in cm.  This is the distance from filament sensor to middle of barrel
#define DEFAULT_NOMINAL_FILAMENT_DIA  3.0  //Enter the diameter (in mm) of the filament generally used (3.0 mm or 1.75 mm) - this is then used in the slicer software.  Used for sensor reading validation
#define MEASURED_UPPER_LIMIT          3.30  //upper limit factor used for sensor reading validation in mm
#define MEASURED_LOWER_LIMIT          1.90  //lower limit factor for sensor reading validation in mm
#define MAX_MEASUREMENT_DELAY			20  //delay buffer size in bytes (1 byte = 1cm)- limits maximum measurement delay allowable (must be larger than MEASUREMENT_DELAY_CM  and lower number saves RAM)
#define DEFAULT_MEASURED_FILAMENT_DIA  DEFAULT_NOMINAL_FILAMENT_DIA  //set measured to nominal initially
#include "Configuration_adv.h"
#include "thermistortables.h"

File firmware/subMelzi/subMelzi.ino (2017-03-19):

/*******
3D Printer Driver Firmware for Melzi board, used as a sub-Melzi
driven by the main Melzi.

Input: 
  Pin A1 is sandstruder stepper step line.
  Pin A2 is 

Output:
  Sandstruder stepper is wired to "E" extruder
  Solenoid tamper is wired to headed bed FET
  Sand shaker is wired to hotend FET

Dr. Orion Lawlor, lawlor@alaska.edu, 2017-02-13 (public domain)
*/

// Constants from http://reprap.org/wiki/Melzi
#define X_STEP_PIN         15
#define X_DIR_PIN          21
#define X_MIN_PIN          18

#define Y_STEP_PIN         22
#define Y_DIR_PIN          23
#define Y_MIN_PIN          19

#define Z_STEP_PIN         3
#define Z_DIR_PIN          2
#define Z_MIN_PIN          20

#define E0_STEP_PIN         1
#define E0_DIR_PIN          0

#define LED_PIN            27

#define FAN_PIN            4 

#define HEATER_0_PIN       13 // extruder heater

#define HEATER_BED_PIN     10 // bed (change to 12 for breakout pin on header)
#define X_ENABLE_PIN       14
#define Y_ENABLE_PIN       14
#define Z_ENABLE_PIN       26
#define E0_ENABLE_PIN      14
#define ENABLE_OFF 1
#define ENABLE_ON 0 /* active low, for some reason */

#define TEMP_0_PIN          7   /* Analog pin */
#define TEMP_BED_PIN        6   /* Analog pin */
#define SDSS               31


// I/O for sandstruder stepper
#define STRUDER_IN_PIN A1
#define STRUDER_ENABLE_PIN E0_ENABLE_PIN
#define STRUDER_STEP_PIN E0_STEP_PIN
#define STRUDER_DIR_PIN E0_DIR_PIN

// I/O for sand shaker
#define SHAKER_PIN HEATER_0_PIN

// I/O for solenoid tamper:
#define TAMPER_IN_PIN A2
#define TAMPER_OUT_PIN FAN_PIN



long last_millis=-10000; // main control loop counter

long last_step_time=-10000; // time we last saw a stepper command
int last_step_val=1;

long first_step_time=-1000; // time this stepper run started
int stepper_running=0;

long last_tamp_time=-10000; // time we last saw a tamper command
int last_tamp_val=1;

void setup(void) {
  Serial.begin(115200);
  Serial.println("Sub-Melzi firmware (lawlor@alaska.edu, 2017-02-14) starting. (kHz)\n");
  pinMode(LED_PIN,OUTPUT); digitalWrite(LED_PIN,1);
  
  // Turn off everything
  pinMode(X_ENABLE_PIN,OUTPUT); digitalWrite(X_ENABLE_PIN,ENABLE_OFF);
  pinMode(Y_ENABLE_PIN,OUTPUT); digitalWrite(Y_ENABLE_PIN,ENABLE_OFF);
  pinMode(Z_ENABLE_PIN,OUTPUT); digitalWrite(Z_ENABLE_PIN,ENABLE_OFF);
  pinMode(HEATER_BED_PIN,OUTPUT); digitalWrite(HEATER_BED_PIN,0);
  pinMode(HEATER_0_PIN,OUTPUT); digitalWrite(HEATER_0_PIN,0);
  
  // Turn on extruder stepper driver
  pinMode(STRUDER_ENABLE_PIN,OUTPUT); digitalWrite(STRUDER_ENABLE_PIN,ENABLE_OFF); // steppers off until commanded
  pinMode(STRUDER_DIR_PIN,OUTPUT); digitalWrite(STRUDER_DIR_PIN,1); // doublecheck direction
  pinMode(STRUDER_STEP_PIN,OUTPUT);
  
  // Hammer solenoid output
  pinMode(TAMPER_OUT_PIN,OUTPUT); digitalWrite(TAMPER_OUT_PIN,0);
  pinMode(SHAKER_PIN,OUTPUT); digitalWrite(SHAKER_PIN,0);
  
  // Input from main Melzi (and pullup to avoid noise)
  pinMode(STRUDER_IN_PIN,INPUT_PULLUP);
  pinMode(TAMPER_IN_PIN,INPUT_PULLUP);
}

void loop(void) {
  unsigned int n_iter=0, n_step=0, n_tamp=0;
  long cur; // current time, in milliseconds (ish, skips every 43ms)
  while (last_millis==(cur=millis())) 
  { // forward stepper commands here: this loop runs at about 130kHz
    n_iter++;
    int step=digitalRead(STRUDER_IN_PIN);
    if (last_step_val!=step) 
    { // stepper moved
      n_step++;
      last_step_val=step;
      digitalWrite(STRUDER_ENABLE_PIN,ENABLE_ON); // steppers on
      digitalWrite(STRUDER_STEP_PIN,step); // forward the step command
    }
    int tamp=digitalRead(TAMPER_IN_PIN);
    if (last_tamp_val!=tamp)
    { // tamper moved
      n_tamp++;
      last_tamp_val=tamp;
    }
  }
  last_millis=cur;
  
  if (n_tamp>2) last_tamp_time=cur; // ignore short tamper blips
  if (n_step>0) {
    last_step_time=cur;
    if (!stepper_running) {
      stepper_running=1;
      first_step_time=cur;
    }
  }

  // Stepper enable logic
  if (cur-last_step_time<10)
  { // stepper is active
    if (((cur-first_step_time)%10000)<500) 
    { // periodically run shaker gently, to redistribute sand
      analogWrite(SHAKER_PIN,400);
    } else {
      digitalWrite(SHAKER_PIN,0);
    }
  } 
  else 
  { // stepper stopped
    stepper_running=0;
    digitalWrite(STRUDER_ENABLE_PIN,ENABLE_OFF); // stepper off (avoid heating)
    digitalWrite(SHAKER_PIN,0);
  // HACK: only tamp if stepper is disabled.  
  //  needed because some Marlin bug randomly whacks the hammer while printing.

    // Tamp logic (every 1ms is plenty)
    bool hammertime=0;
    if (cur-last_tamp_time<10) 
    { // run tamping hammer
      hammertime=1;
      int period=64; // tamping cycle time in ms
      int on_time=7; // duty cycle: ms of on time during each cycle. 6 is min at 20v bus.
      int tamper=(cur%period <= on_time); // timing based
      digitalWrite(TAMPER_OUT_PIN,tamper);
      digitalWrite(LED_PIN,tamper); // fast blink to indicate tamping active
    } else { // now stop
      digitalWrite(TAMPER_OUT_PIN,0); // tamper off
    }
  }
  
  // Debug printouts: kHz rate, minus if tamping.
  if (cur%512==0) {
    // if (hammertime) iter=-iter;
    Serial.println(n_iter);
  }
  
  // Alive indicator blinking.
  int blink=(cur%2048)<100;
  digitalWrite(LED_PIN,blink);
}

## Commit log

2014-11-11 Added a bunch of inch vitamins, and extremely beefy "lawlor90" config.
    [hot_ends.scad, lawlor90_config.scad, linear-bearings.scad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]
2014-11-12 Initial design with 600mm travels. I'm really getting excited about this!
    [lawlor90_config.scad]
2014-11-12 Fixed z_bar_offset() to account for bigger guides and nuts; about to rotate Z bar clamps for strength.
    [config.scad, lawlor90_config.scad, nuts.scad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]
2014-11-12 Rotate Z motor's bracket clamp orientation.
    [z-motor-bracket.scad]
2014-11-12 Added module z_motor_bracket_orient() to be able to move around bracket orientation.
    [z-motor-bracket.scad]
2014-11-12 Fattened up Z motor bracket, to better support big guide rods.
    [positions.scad, z-motor-bracket.scad]
2014-11-12 Ugly hacks to fatten up Y belt anchor.
    [y-belt-anchor.scad, z-motor-bracket.scad]
2014-11-12 Fixed spacing between Y bars to be closer together, instead of weak at far sides.
    [lawlor90_config.scad, main.scad]
2014-11-16 Mods for prints 1 -> prints 2: thicker wall on bearing holder, bigger zipties.
    [bearing-holder.scad, ziptie.scad]
2014-11-17 Add fillets to Y and Z bar clamps, and fix non-manifold cal object.
    [bar-clamp.scad, bearing-holder.scad, cal.scad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]
2014-11-27 Cut holes to let zipties fit in carriage, and eliminate weird gap between carriage and slides.
    [x-carriage.scad]
2014-11-27 Added Chinese J-head clone info to wade block.
    [hot_ends.scad, lawlor90_config.scad, wade.scad]
2014-11-29 Added an adjustable holder for 22mm 608 skate bearing, and renamed machine as "alaska90".
    [alaska90_config.scad, y_adjustable_holder.scad]
2015-08-06 Last few changes before merge.
    [machine.scad, pulley.stl, pulley_meatier.scad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]
2015-08-06 Added middle mounting bracket. This was a field addition to reduce Y axis deflection on the 48 inch run.
    [bar-clamp.scad]
2015-08-06 Add new pulley_type field. Still using T5 pulleys.
    [alaska90_config.scad]
2015-08-06 Added build of the alaska90, for people to see and try without touching OpenSCAD. You'll generate these yourself with "./make_machine.py alaska90", which lets you change the SCAD files.
    [atx_brackets.stl, atx_long_bracket.stl, atx_short_bracket.stl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]
2015-08-06 Added photo of printer in action.
2015-11-29 Added initial version of firmware. This includes the 8-tooth pulleys, that slowly break T5 belts.
    [Configuration.h, Configuration_adv.h, Configuration_factory_default.h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]
2015-11-30 Fixed config files for 12 tooth pulleys.
    [Configuration.h]
2015-11-30 With the new bigger pulleys, at my old acceleration settings Y steps are lost. Backing them off this far does not lose steps.
    [Configuration.h]
2016-06-14 Working well with big bed. About to tune sizes.
    [Configuration.h]
2017-02-18 Retune for 20V operation.
    [Configuration.h]
2017-02-19 Update firmware for sandstruder support: pin A1 of main Melzi couples to pin A1 of sub Melzi. When A1 blips, subMelzi runs tamper and stepper. gcode support for this is "t0" (tool 0, extruder), and "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
    [Configuration.h]
2017-03-05 Updated to three-extruder configuration. This exposes a weird bug in Marlin (T2 jiggles as T1 extrudes), but I can compensate in the subMelzi firmware (filter short spikes)
    [Configuration.h]
2017-03-14 Updated toolhead offsets for new mounting setup.
    [Configuration.h]
2017-03-19 Tuned for faster motion at 24VDC. It's scary fast now!
    [Configuration.h]
2017-03-19 Added more info on building for Melzi board, and initial shaker support.
2017-03-24 Use more conservative speeds & acceleration on Y axis, which is losing steps.
    [Configuration.h]
2017-05-07 Add skate bearing based Y axis. This is needed for heavy beds when the Y rods are weird sizes.
    [y-bearing-mount-skate.scad]
2017-05-08 Thicken up wade's block mount, and use nylock M3 nuts to mount the hotend more reliably.
    [config.scad, hot_ends.scad, jhead_hot_end.scad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]
